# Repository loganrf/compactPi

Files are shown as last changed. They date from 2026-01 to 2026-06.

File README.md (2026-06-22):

# compactPi

compactPi is a project to develop a compact Raspberry Pi Compute Module carrier suitable for ArduPilot applications. It's primarily targeted at marine applications (ArduSub/ArduRover).

## Milestones

As of June 2026, these milestones are way out of date due to personal circumstances. As I get back up to speed there will be substantial updates to this timeline!

| # | Description | Estimated Time Frame| Status |
|---|---|---|---|
| 1 |Feature freeze | Mid-Feb | On Track |
| 2 |Schematic/layout draft ready for review | Early march | In Work |
| 3 |Gerbers ready for review | End of march | TBD |
| 4 |PCB Tape Out | Mid April | TBD |
| 5 |Board Fab & Build | June/July (assuming 30 day turn for initial prototypes to keep costs maneagable)| TBD |
| 6 |Validation/Verification Complete| TBD | TBD |
| 7 |V1.0 Design File Release| TBD (dependent on how well the first rev does) | TBD |

# Layout Study (PRELIMINARY)
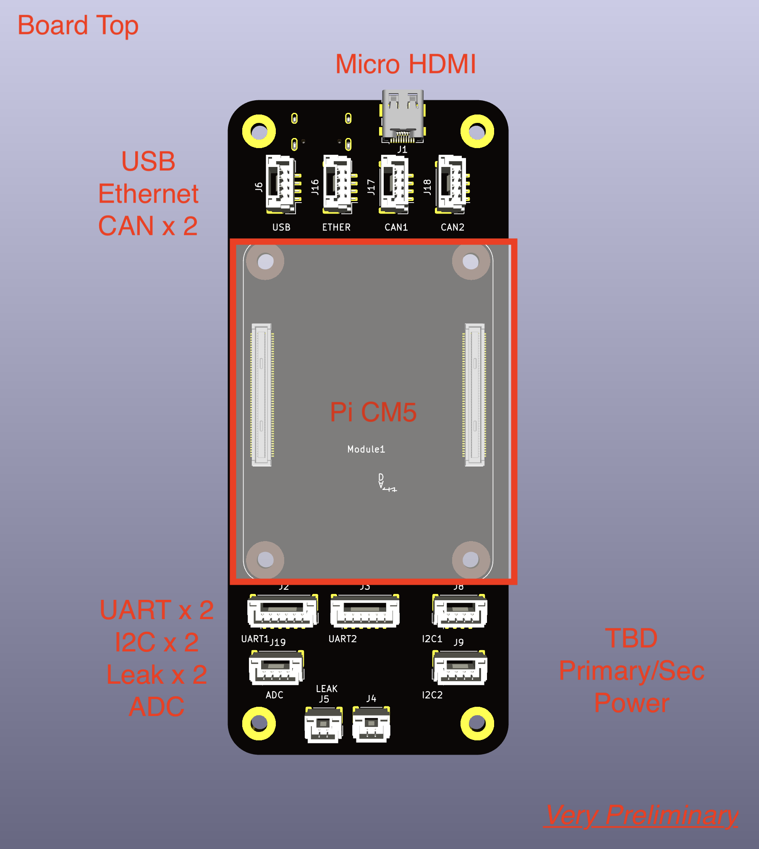
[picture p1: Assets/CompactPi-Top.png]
Top

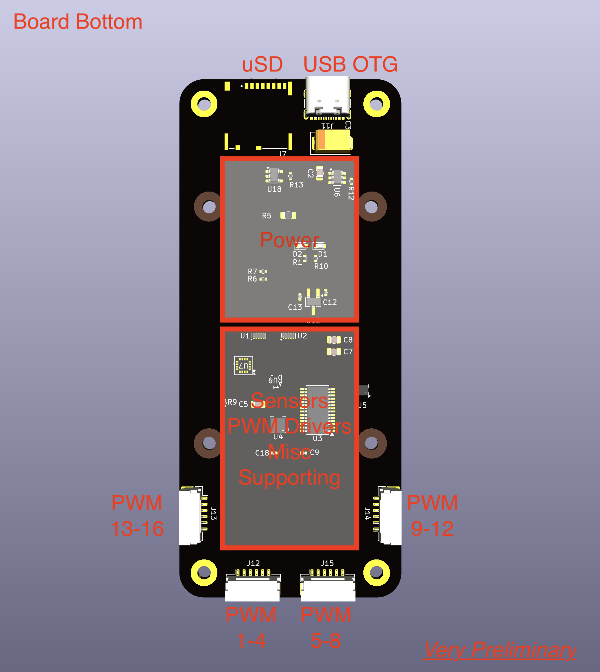
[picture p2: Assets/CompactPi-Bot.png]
Bottom


# Design Details (PROPOSED)

## Power/Physical
| # | Description | Value/Units | Notes |
|---|---|---|---|
| 1 |Input Voltage range| 6-25V | 2 independent inputs + USB-C PD option |
| 2 |Mainboard power dissipation | 25W | |
| 3 |Dimensions | 45mm x 105mm | Evaluating options for shrinking length without over-crowding connectors|

## Key Sensors
| # | Description | Part Number | 
|---|---|---|
| 1 |6 Axis IMU | ICM-20602 |
| 2 |3 Axis Magnetometer | MMC5983 |
| 3 |3 Axis Compass | AK09915 |
| 4 |Barometer | BMP280 |
| 5 |ADC | TBD |

## Interfaces
| # | Description | Form Factor | Qty | Notes |
|---|---|---|---|---|
| 1 |UART | JST-GH BM06B | 2 |  |
| 2 |I2C | JST-GH BM04B | 2 |  |
| 3 |SBUS | TBD |1| |
| 4 |5V PWM Quad Out | JST-GH BM06B | 4 | 4 PWM channels per connector, 16 total per carrier|
| 5 |Leak Sensor | JST-GH BM02B | 1 | |
| 6 |ADC | TBD | TBD| |
| 7 |HDMI | HDMI-C | 1 | |
| 8 |Ethernet 10/100| JST-GH BM04B | 1 | |
| 9 |USB| 1x JST-GH BM04B/ 1x USB-C OTG | 2 | |
| 10 |SD| micro-SD | 1 | |
| 11 |Power | TBD | 2 | |
| 12 |CAN Bus | JST-GH BM04B | 2 | |

# Stackup
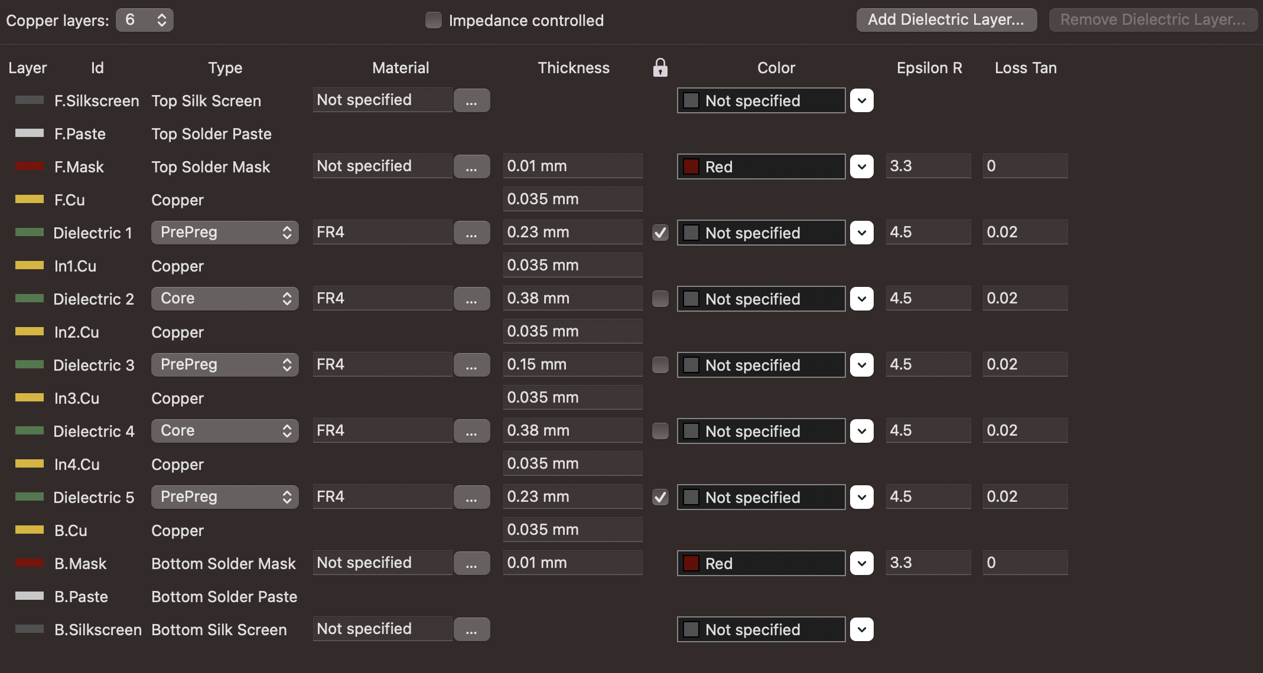
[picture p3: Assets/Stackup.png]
Stackup Diagram From KiCAD


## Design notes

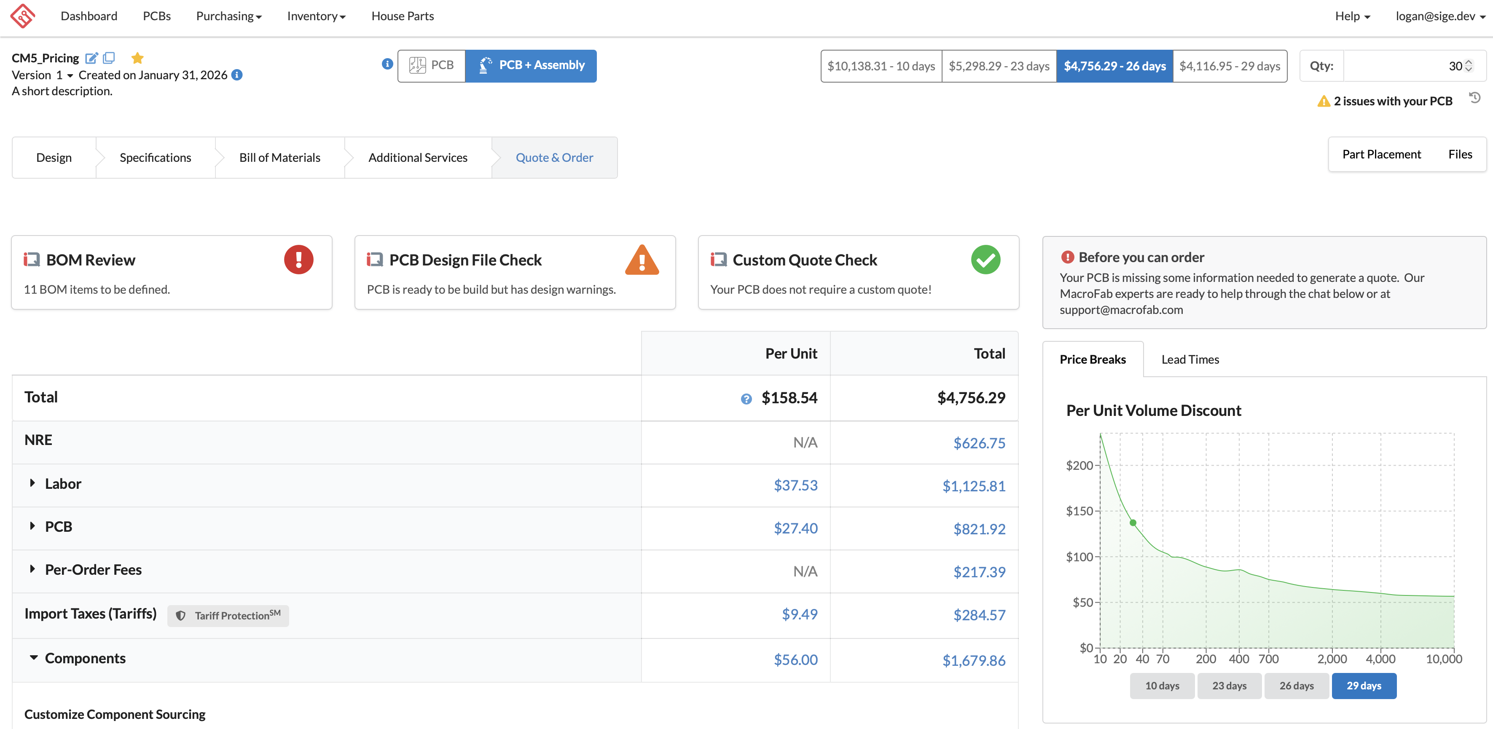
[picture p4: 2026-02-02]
Docs/Screenshot 2026-01-31 at 20.46.59.png

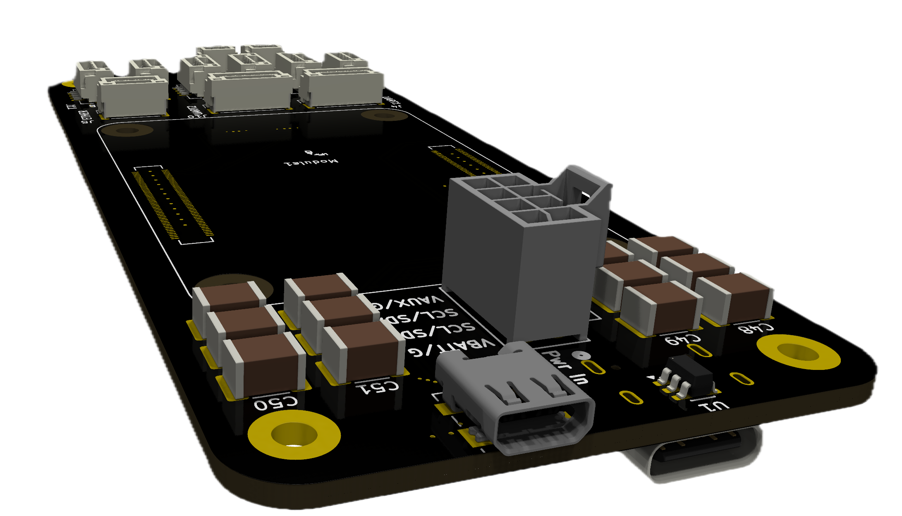
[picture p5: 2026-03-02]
Docs/compactPi-angle.png

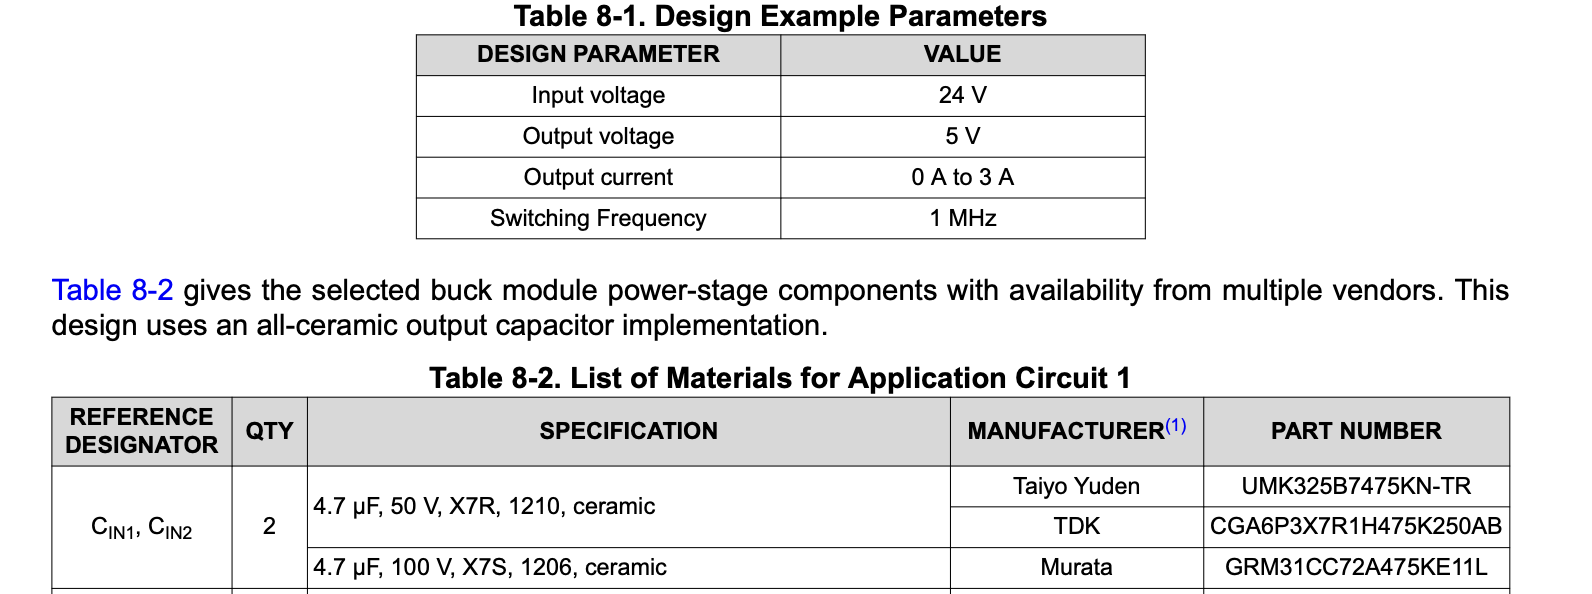
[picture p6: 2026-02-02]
Docs/Screenshot 2026-02-01 at 09.07.32.png

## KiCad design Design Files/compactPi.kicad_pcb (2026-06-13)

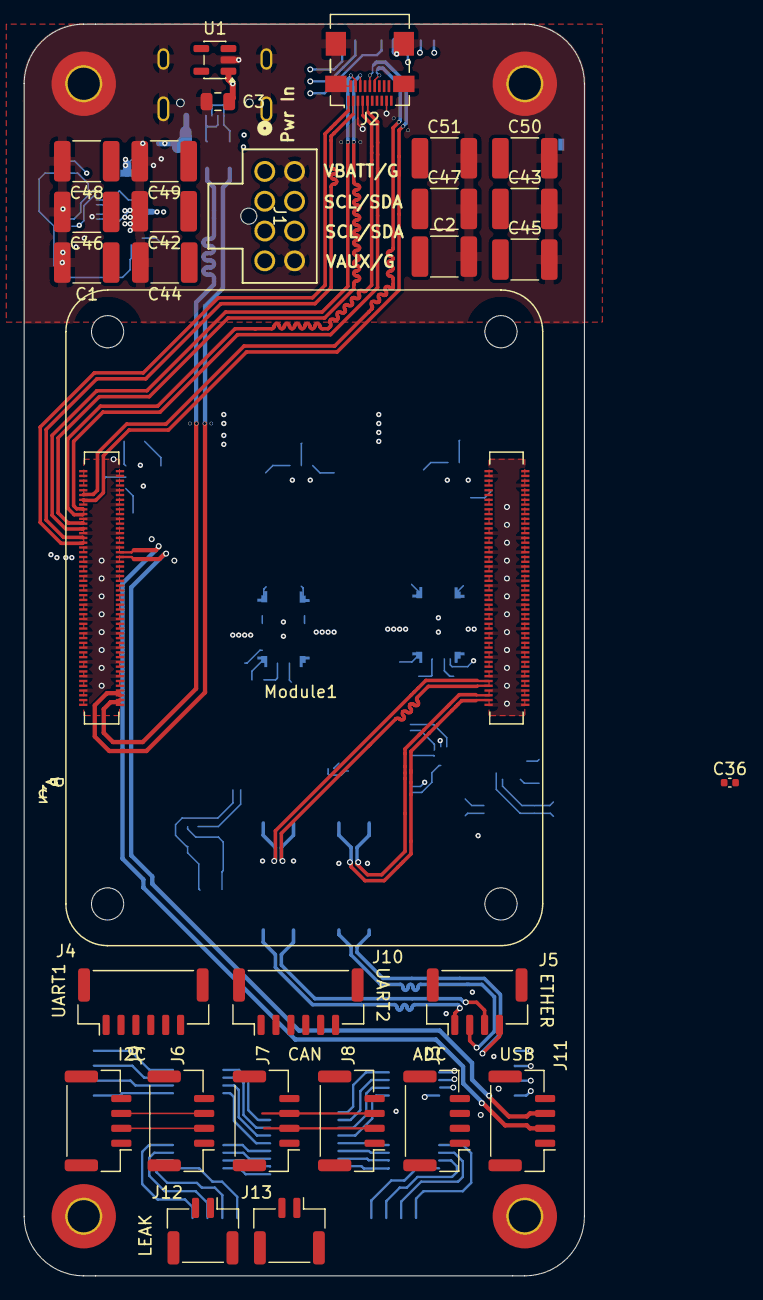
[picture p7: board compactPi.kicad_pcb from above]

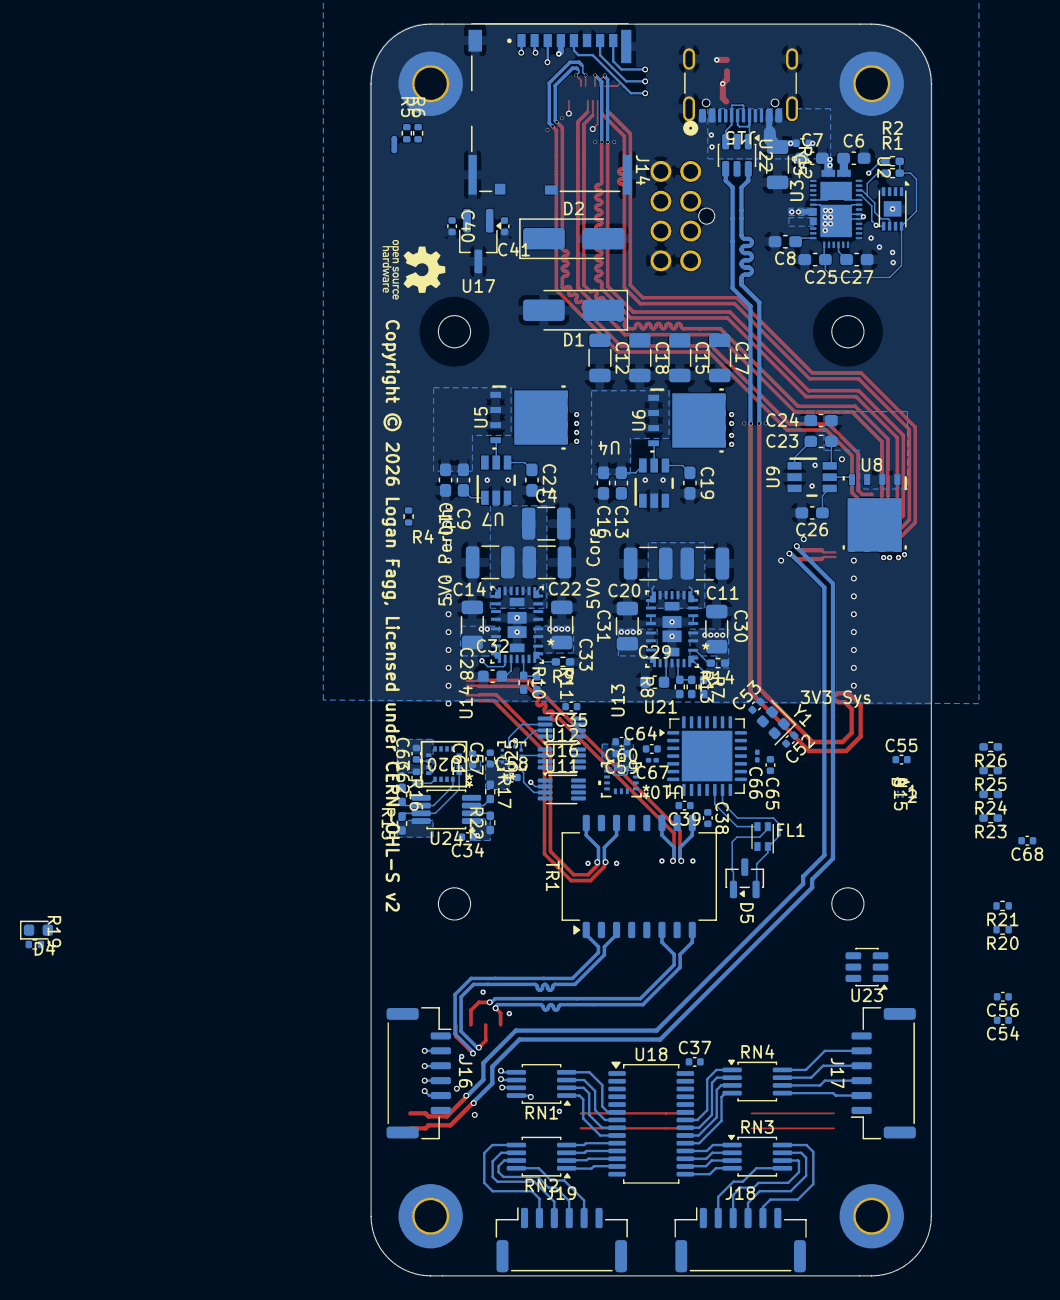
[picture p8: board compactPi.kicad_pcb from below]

Board: 6 copper layers, 47.0 x 105.0 mm, 152 parts (119 on the bottom side), 144 nets.

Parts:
C1, C2, C42, C43, C44, C45, C46, C47, C48, C49, C50, C51: 6.8uF; C_1812_4532Metric
C3: 10u; C_0805_2012Metric
C4, C11, C14, C20, C22: 47uF; C_1210_3225Metric
C5, C12, C15, C17, C18, C28, C30, C31, C33: 4.7uF; C_1206_3216Metric
C6, C7, C8, C9, C10, C13, C16, C19, C21, C23, C24, C25, C26, C27: 100nF; C_0603_1608Metric_Pad1.08x0.95mm_HandSolder
C29, C32: 1uF; C_0603_1608Metric
C34, C35, C36, C37, C38, C39, C54, C55, C57, C58, C59, C60, C61, C62, C64, C65: 100nF; C_0402_1005Metric
C40, C41: 100n; C_0402_1005Metric
C52, C53: 22pF; C_0402_1005Metric
C56: 1000pF; C_0402_1005Metric
C63: 10uF; C_0402_1005Metric
C66, C67: 10u; C_0201_0603Metric
C68: 47pF; C_0402_1005Metric
D1, D2: SMAJ26A; D_SMA_Handsoldering
D4: LED Red; LED_0603_1608Metric
D5: SZNUP2105L; SOT-23
FL1: Choke_CommonMode_FerriteCore_1234; L_CommonModeChoke_Coilcraft_0805USB
H1, H2, H3, H4: MountingHole_Pad; MountingHole_2.7mm_Pad_TopBottom
J1: 1053101208; CONN_SD-105310-100_08_MOL
J2: HDMI_A_1.4; HDMI_Micro-D_Molex_46765-0xxx
J3, J5, J6, J7, J8, J9, J11: Conn_01x04_MountingPin; JST_GH_BM04B-GHS-TBT_1x04-1MP_P1.25mm_Vertical
J4, J10: Conn_01x06_MountingPin; JST_GH_BM06B-GHS-TBT_1x06-1MP_P1.25mm_Vertical
J12, J13: Conn_01x02_MountingPin; JST_GH_BM02B-GHS-TBT_1x02-1MP_P1.25mm_Vertical
J14: Micro_SD_Card_Det; SDCARD_MOLEX_503398-1892
J15: USB_C_Receptacle_USB2.0; USB_C_Receptacle_GCT_USB4105-xx-A_16P_TopMnt_Horizontal
J16, J17, J18, J19: Conn_01x06_MountingPin; JST_GH_SM06B-GHS-TB_1x06-1MP_P1.25mm_Horizontal
Module1: ComputeModule5-CM5; Raspberry-Pi-5-Compute-Module
NT1: NetTie_2; NetTie-2_SMD_Pad0.5mm
R1, R2: R_US; R_0402_1005Metric_Pad0.72x0.64mm_HandSolder
R4: 10K 1%; R_0402_1005Metric
R5, R6, R12: 2.2K 1%; R_0402_1005Metric
R7, R9: 25.5k; R_0402_1005Metric_Pad0.72x0.64mm_HandSolder
R8, R11, R14, R15, R16, R17, R22, R23, R24, R26: 10k; R_0402_1005Metric_Pad0.72x0.64mm_HandSolder
R10, R13: 53.6k; R_0402_1005Metric_Pad0.72x0.64mm_HandSolder
R19: 1k; R_0402_1005Metric
R20, R21: 75; R_0402_1005Metric
R25: 120; R_0402_1005Metric_Pad0.72x0.64mm_HandSolder
RN1, RN2, RN3, RN4: R_Pack04; MSOP-8_3x3mm_P0.65mm
TR1: TG110-E050N5xx; Transformer_Ethernet_Halo_N5_SO-16_7.11x12.7mm
U1: RT9742GGJ5; SOT-23-5
U2: AT24CS64-MAHM; DFN-8-1EP_3x2mm_P0.5mm_EP1.3x1.5mm
U3: TPS25751D
U4, U7, U9: LM74700QDBVRQ1; DBV0006A_M
U5, U6, U8: CSD18511Q5A; DQJ0008A
U10: BMI270; BMI270_BOS
U11, U12, U16: 74LVC2T45DC; VSSOP-8_2.3x2mm_P0.5mm
U13, U14: TLVM13630RDHR; B0QFN30_RDH_TEX
U15: AK09918C; BGA4_WL-CSP_AKM
U17: RT9742SNGV; TSOT-23_HandSoldering
U18: PCA9685PW; TSSOP-28_4.4x9.7mm_P0.65mm
U20: MMC5983MA; MMC5983MA_MEM
U21: MCP25625x-x-ML; QFN-28-1EP_6x6mm_P0.65mm_EP4.25x4.25mm
U22, U23: WE-TVS-82400102; SOT-23-6
U24: TCA9517ADGK; VSSOP-8_3x3mm_P0.65mm
U25: BMP390; 10LGA_2X2X0p75_BOS
Y1: Crystal_GND24_Small; Crystal_SMD_2016-4Pin_2.0x1.6mm

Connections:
/1V8: C34.1, C55.1, C57.1, C58.1, C59.1, C60.1, Module1.88 (+1.8v_(Output)), Module1.90 (+1.8v_(Output)), R17.1, R22.1, U10.5 (VDDIO), U10.8 (VDD), U11.1 (VCCA), U12.1 (VCCA), U15.B1 (VDD), U16.8 (VCCB), U24.1 (VCCA), U25.1 (VDDIO), U25.10 (VDD)
/3V3: C35.1, C36.1, C37.1, C38.1, C39.1, C61.1, D4.2 (A), Module1.84 (+3.3v_(Output)), Module1.86 (+3.3v_(Output)), NT1.1, R4.1, R15.1, R16.1, R26.2, U1.5 (IN), U11.8 (VCCB), U12.8 (VCCB), U16.1 (VCCA), U18.28 (VDD), U20.2 (VDD), U21.11 (V_{IO}), U24.8 (VCCB)
/5V0_CORE: Module1.77 (+5v_(Input)), Module1.79 (+5v_(Input)), Module1.81 (+5v_(Input)), Module1.83 (+5v_(Input)), Module1.85 (+5v_(Input)), Module1.87 (+5v_(Input))
/5V0_PERIPHERAL: C41.1, C64.1, C65.1, C66.1, C67.1, J4.1, J6.1, J7.1, J8.1, J9.1, J10.1, J11.1, J16.1, J17.1, J18.1, J19.1, U17.1 (IN), U21.3 (V_{DD}), U21.19 (V_{DDA})
/Autopilot Interfaces/CANH_PC: FL1.1, U21.13 (CANH)
/Autopilot Interfaces/CAN_CLKO: C68.1, U21.6 (CLKOUT)
/Autopilot Interfaces/CAN_H: D5.1 (K), FL1.2, J7.2, J8.2, R25.1
/Autopilot Interfaces/CAN_L: D5.2 (K), FL1.4, J7.3, J8.3, R25.2
/Autopilot Interfaces/CAN_L_PC: FL1.3, U21.12 (CANL)
/Autopilot Interfaces/CAN_PULL_HI: R26.1, U21.7 (~Tx0RTS), U21.8 (~Tx1RTS), U21.9 (~Tx2RTS), U21.23 (~Rx1BF), U21.24 (~Rx0BF)
/Autopilot Interfaces/CAN_RST: R23.1, U21.2 (~RESET)
/Autopilot Interfaces/CAN_RX: U21.5 (RxCAN), U21.10 (R_{XD})
/Autopilot Interfaces/CAN_STBY: R24.1, U21.15 (STBY)
/Autopilot Interfaces/CAN_TX: U21.4 (TxCAN), U21.16 (T_{XD})
/Autopilot Interfaces/OSC_1: C53.1, U21.21 (OSC1), Y1.3
/Autopilot Interfaces/OSC_2: C52.1, U21.20 (OSC2), Y1.1
/Autopilot Sensors/CS_PRES_1V8: U11.2 (1A), U25.6 (CSB)
/Autopilot Sensors/I2C_SCL_1V8: R22.2, U10.13 (SCX), U15.A2 (SCL), U24.2 (SCLA)
/Autopilot Sensors/I2C_SDA_1V8: R17.2, U10.14 (SDX), U15.B2 (SDA), U24.3 (SDAA)
/Autopilot Sensors/INT_PRES_1V8: U16.6 (2B), U25.7 (INT)
/Autopilot Sensors/MAG_VDDIO: C62.1, U20.13 (VDDIO)
/Autopilot Sensors/SPI_CIPO_1V8: U16.7 (1B), U25.5 (SDO)
/Autopilot Sensors/SPI_COPI_1V8: U12.2 (1A), U25.4 (SDI)
/Autopilot Sensors/SPI_SCK_1V8: U11.3 (2A), U25.2 (SCK)
/CM5 GPIO Ethernet SDIO/GPIO_VREF: Module1.78 (GPIO_VREF(1.8v/3.3v_Input)), NT1.2, R5.1, R6.1
/CM5 GPIO Ethernet SDIO/ID_SC: Module1.35 (ID_SC), R6.2
/CM5 GPIO Ethernet SDIO/ID_SD: Module1.36 (ID_SD), R5.2
/CM5 GPIO Ethernet SDIO/SD_CLK: J14.5 (CLK), Module1.57 (SD_CLK)
/CM5 GPIO Ethernet SDIO/SD_CMD: J14.3 (CMD), Module1.62 (SD_CMD)
/CM5 GPIO Ethernet SDIO/SD_DAT0: J14.7 (DAT0), Module1.63 (SD_DAT0)
/CM5 GPIO Ethernet SDIO/SD_DAT1: J14.8 (DAT1), Module1.67 (SD_DAT1)
/CM5 GPIO Ethernet SDIO/SD_DAT2: J14.1 (DAT2), Module1.69 (SD_DAT2)
/CM5 GPIO Ethernet SDIO/SD_DAT3: J14.2 (DAT3/CD), Module1.61 (SD_DAT3)
/CM5 GPIO Ethernet SDIO/SD_PWR: C3.1, J14.4 (VDD), U1.1 (OUT)
/CM5 GPIO Ethernet SDIO/SD_PWR_ON: Module1.75 (SD_PWR_ON), R4.2, U1.4 (EN)
/CM5 GPIO Ethernet SDIO/TRD0_N: Module1.10 (Ethernet_Pair0_N), TR1.11 (RD-)
/CM5 GPIO Ethernet SDIO/TRD0_P: Module1.12 (Ethernet_Pair0_P), TR1.9 (RD+)
/CM5 GPIO Ethernet SDIO/TRD0_TX_N: J5.3, TR1.6 (RX-)
/CM5 GPIO Ethernet SDIO/TRD0_TX_P: J5.1, TR1.8 (RX+)
/CM5 GPIO Ethernet SDIO/TRD1_N: Module1.6 (Ethernet_Pair1_N), TR1.16 (TD-)
/CM5 GPIO Ethernet SDIO/TRD1_P: Module1.4 (Ethernet_Pair1_P), TR1.14 (TD+)
/CM5 GPIO Ethernet SDIO/TRD1_RX_N: J5.4, TR1.1 (TX-)
/CM5 GPIO Ethernet SDIO/TRD1_RX_P: J5.2, TR1.3 (TX+)
/CM5 GPIO Ethernet SDIO/nPWR_LED: Module1.95 (LED_nPWR), R19.2
/CM5 USB HDMI/HDMI0_CEC: J2.13 (CEC), Module1.151 (HDMI0_CEC)
/CM5 USB HDMI/HDMI0_CK_N: J2.12 (CK-), Module1.190 (HDMI0_CLK_N)
/CM5 USB HDMI/HDMI0_CK_P: J2.10 (CK+), Module1.188 (HDMI0_CLK_P)
/CM5 USB HDMI/HDMI0_D0_N: J2.9 (D0-), Module1.184 (HDMI0_TX0_N)
/CM5 USB HDMI/HDMI0_D0_P: J2.7 (D0+), Module1.182 (HDMI0_TX0_P)
/CM5 USB HDMI/HDMI0_D1_N: J2.6 (D1-), Module1.178 (HDMI0_TX1_N)
/CM5 USB HDMI/HDMI0_D1_P: J2.4 (D1+), Module1.176 (HDMI0_TX1_P)
/CM5 USB HDMI/HDMI0_D2_N: J2.3 (D2-), Module1.172 (HDMI0_TX2_N)
/CM5 USB HDMI/HDMI0_D2_P: J2.1 (D2+), Module1.170 (HDMI0_TX2_P)
/CM5 USB HDMI/HDMI0_HOTPLUG: J2.19 (HPD/HEAC-), Module1.153 (HDMI0_HOTPLUG)
/CM5 USB HDMI/HDMI0_SCL: J2.15 (SCL), Module1.200 (HDMI0_SCL)
/CM5 USB HDMI/HDMI0_SDA: J2.16 (SDA), Module1.199 (HDMI0_SDA)
/CM5 USB HDMI/HDMI_5v: C40.1, J2.18 (+5V), U17.2 (OUT)
/CM5 USB HDMI/USB3-1-D_N: J11.2, Module1.165 (USB3-1-D_N)
/CM5 USB HDMI/USB3-1-D_P: J11.3, Module1.163 (USB3-1-D_P)
/I2C_EXT_SCL1: J6.2, J9.2, Module1.56 (GPIO3)
/I2C_EXT_SDA1: J6.3, J9.3, Module1.58 (GPIO2)
/I2C_INT_SCL0: Module1.80 (SCL0), R15.2, U20.1 (SCL/SPI_SCK), U24.7 (SCLB)
/I2C_INT_SDA0: Module1.82 (SDA0), R16.2, U20.16 (SDA/SPI_SDI), U24.6 (SDAB)
/I2C_PWM_SCL: Module1.37 (GPIO7), U18.26 (SCL)
/I2C_PWM_SDA: Module1.30 (GPIO6), U18.27 (SDA)
/PWM IO/PWM_01_PR: RN1.3 (R3.1), U18.7 (LED1)
/PWM IO/PWM_02_PR: RN1.2 (R2.1), U18.8 (LED2)
/PWM IO/PWM_03_PR: RN1.1 (R1.1), U18.9 (LED3)
/PWM IO/PWM_04_PR: RN2.4 (R4.1), U18.10 (LED4)
/PWM IO/PWM_05_PR: RN2.3 (R3.1), U18.11 (LED5)
/PWM IO/PWM_06_PR: RN2.2 (R2.1), U18.12 (LED6)
/PWM IO/PWM_07_PR: RN2.1 (R1.1), U18.13 (LED7)
/PWM IO/PWM_08_PR: RN3.4 (R4.1), U18.15 (LED8)
/PWM IO/PWM_09_PR: RN3.3 (R3.1), U18.16 (LED9)
/PWM IO/PWM_10_PR: RN3.2 (R2.1), U18.17 (LED10)
/PWM IO/PWM_11_PR: RN3.1 (R1.1), U18.18 (LED11)
/PWM IO/PWM_12_PR: RN4.4 (R4.1), U18.19 (LED12)
/PWM IO/PWM_13_PR: RN4.3 (R3.1), U18.20 (LED13)
/PWM IO/PWM_14_PR: RN4.2 (R2.1), U18.21 (LED14)
/PWM IO/PWM_15_PR: RN4.1 (R1.1), U18.22 (LED15)
/PWM IO/PWM_PR_00: RN1.4 (R4.1), U18.6 (LED0)
/Power/5V0_C_FB: R8.1, R13.2, U13.25 (FB)
/Power/5V0_C_RAW: C11.1, C20.1, R13.1, U13.7 (VOUT), U13.8 (VOUT), U13.9 (VOUT), U13.10 (VOUT), U13.12 (VOUT), U13.13 (VOUT), U13.14 (VOUT), U13.15 (VOUT), U13.22 (VLDOIN), U13.30 (VOUT)
/Power/5V0_C_RT: R7.1, U13.1 (RT)
/Power/5V0_C_VCC: C29.1, U13.23 (VCC)
/Power/5V0_EN: R14.2, U13.2 (EN/SYNC)
/Power/5V0_P_FB: R10.2, R11.1, U14.25 (FB)
/Power/5V0_P_RAW: C4.1, C14.1, C22.1, R10.1, U14.7 (VOUT), U14.8 (VOUT), U14.9 (VOUT), U14.10 (VOUT), U14.12 (VOUT), U14.13 (VOUT), U14.14 (VOUT), U14.15 (VOUT), U14.22 (VLDOIN), U14.30 (VOUT)
/Power/5V0_P_RT: R9.1, U14.1 (RT)
/Power/5V0_P_VCC: C32.1, U14.23 (VCC)
/Power/5V_PERIPHERAL: U3.34 (PP5V), U3.35 (PP5V)
/Power/I2Cc_SCL: R1.2, U2.6 (SCL), U3.17 (I2Cc_SCL)
/Power/I2Cc_SDA: R2.2, U2.5 (SDA), U3.16 (I2Cc_SDA)
/Power/LDO_1V5: C27.1, U3.4 (LDO_1V5)
/Power/USB_DRAIN: U3.15 (DRAIN), U3.30 (DRAIN), U3.40 (DRAIN_PAD)
/Power/USB_LDO_3V3: C25.1, R1.1, R2.1, U2.8 (VCC), U3.1 (LDO_3V3)
/Power/VIN_3V3: C8.1, U3.38 (VIN_3V3)
/Power/V_AUX: C2.1, C12.1, C13.1, C16.1, C18.1, C43.1, C45.1, C47.1, C50.1, C51.1, D1.1 (A1), J1.4, U4.3 (EN), U4.6 (ANODE), U6.1 (S), U6.2 (S), U6.3 (S)
/Power/V_BATT: C1.1, C9.1, C10.1, C15.1, C17.1, C42.1, C44.1, C46.1, C48.1, C49.1, D2.1 (A1), J1.1, U5.1 (S), U5.2 (S), U5.3 (S), U7.3 (EN), U7.6 (ANODE)
/Power/V_COMMON: C19.1, C21.1, C26.1, C28.1, C30.1, C31.1, C33.1, R14.1, U4.4 (CATHODE), U5.5 (D), U5.6 (D), U5.7 (D), U5.8 (D), U5.9 (D), U6.5 (D), U6.6 (D), U6.7 (D), U6.8 (D), U6.9 (D), U7.4 (CATHODE), U8.5 (D), U8.6 (D), U8.7 (D), U8.8 (D), U8.9 (D), U9.4 (CATHODE), U13.3 (VIN), U13.4 (VIN), U13.18 (VIN), U13.19 (VIN), U14.3 (VIN), U14.4 (VIN), U14.18 (VIN), U14.19 (VIN)
/Power/V_USB: C6.1, C23.1, C24.1, U3.20 (PPHV), U3.21 (PPHV), U3.22 (PPHV), U8.1 (S), U8.2 (S), U8.3 (S), U9.3 (EN), U9.6 (ANODE)
/SPI_CAN_CE0: Module1.49 (GPIO18), U21.1 (~CS)
/SPI_CAN_CIPO: Module1.27 (GPIO20), U21.28 (SO)
/SPI_CAN_COPI: Module1.26 (GPIO19), U21.27 (SI)
/SPI_CAN_SCK: Module1.25 (GPIO21), U21.26 (SCK)
/SPI_INT_CE0: Module1.39 (GPIO8), U11.7 (1B)
/SPI_INT_CIPO: Module1.44 (GPIO10), U16.2 (1A)
/SPI_INT_COPI: Module1.40 (GPIO9), U12.7 (1B)
/SPI_INT_SCK: Module1.38 (GPIO11), U11.6 (2B)
/USB2_N: J15.A7 (D-), J15.B7 (D-), U22.1
/USB2_P: J15.A6 (D+), J15.B6 (D+), U22.3
/USB2a_N: Module1.103 (USB2_N), U22.6
/USB2a_P: Module1.105 (USB2_P), U22.4
/VBUS: C5.1, C7.1, J15.A4 (VBUS), J15.A9 (VBUS), J15.B4 (VBUS), J15.B9 (VBUS), R12.1, U3.23 (VBUS_IN), U3.24 (VBUS_IN), U3.25 (VBUS_IN), U3.32 (VBUS), U3.33 (VBUS)
/VBUS_EN: Module1.111 (VBUS_EN), U14.2 (EN/SYNC)
GND: C1.2, C2.2, C3.2, C4.2, C5.2, C6.2, C7.2, C8.2, C10.2, C11.2, C12.2, C14.2, C15.2, C16.2, C17.2, C18.2, C19.2, C20.2, C21.2, C22.2, C24.2, C25.2, C26.2, C27.2, C28.2, C29.2, C30.2, C31.2, C32.2, C33.2, C34.2, C35.2, C36.2, C37.2, C38.2, C39.2, C40.2, C41.2, C42.2, C43.2, C44.2, C45.2, C46.2, C47.2, C48.2, C49.2, C50.2, C51.2, C52.2, C53.2, C54.2, C55.2, C56.2, C57.2, C58.2, C59.2, C60.2, C61.2, C62.2, C63.2, C64.2, C65.2, C66.2, C67.2, C68.2, D1.2 (A2), D2.2 (A2), D5.3 (A), H1.1 (1_1), H2.1 (1_1), H3.1 (1_1), H4.1 (1_1), J1.5, J1.8, J2.2 (D2S), J2.5 (D1S), J2.8 (D0S), J2.11 (CKS), J2.17 (GND), J2.SH, J4.6, J6.4, J7.4, J8.4, J9.4, J10.6, J11.4, J14.6 (VSS), J14.11 (SHIELD), J15.A1 (GND), J15.A12 (GND), J15.B1 (GND), J15.B12 (GND), J15.S1 (SHIELD), J16.6, J17.6, J18.6, J19.6, Module1.1 (GND), Module1.2 (GND), Module1.7 (GND), Module1.8 (GND), Module1.13 (GND), Module1.14 (GND), Module1.22 (GND), Module1.23 (GND), Module1.32 (GND), Module1.33 (GND), Module1.42 (GND), Module1.43 (GND), Module1.52 (GND), Module1.53 (GND), Module1.59 (GND), Module1.60 (GND), Module1.65 (GND), Module1.66 (GND), Module1.71 (GND), Module1.74 (GND), Module1.93 (nRPIBOOT), Module1.98 (GND), Module1.107 (GND), Module1.108 (GND), Module1.113 (GND), Module1.114 (GND), Module1.119 (GND), Module1.120 (GND), Module1.125 (GND), Module1.126 (GND), Module1.131 (GND), Module1.132 (GND), Module1.137 (GND), Module1.138 (GND), Module1.144 (GND), Module1.150 (GND), Module1.155 (GND), Module1.156 (GND), Module1.161 (GND), Module1.162 (GND), Module1.167 (GND), Module1.168 (GND), Module1.173 (GND), Module1.174 (GND), Module1.179 (GND), Module1.180 (GND), Module1.185 (GND), Module1.186 (GND), Module1.191 (GND), Module1.192 (GND), Module1.197 (GND), Module1.198 (GND), R7.2, R8.2, R9.2, R11.2, R12.2, R23.2, R24.2, U1.2 (GND), U2.4 (GND), U2.9 (GND), U3.11 (GND), U3.12 (GND), U3.14 (GND), U3.31 (GND), U3.39 (GND), U4.2 (GND), U7.2 (GND), U9.2 (GND), U10.6 (GNDIO), U10.7 (GND), U11.4 (GND), U11.5 (DIR), U12.4 (GND), U12.5 (DIR), U12.6 (2B), U13.5 (PGND), U13.6 (PGND), U13.16 (PGND), U13.17 (PGND), U13.24 (AGND), U13.26 (PG), U13.27 (AGND), U13.28 (PGND), U13.29 (PGND), U14.5 (PGND), U14.6 (PGND), U14.16 (PGND), U14.17 (PGND), U14.24 (AGND), U14.26 (PG), U14.27 (AGND), U14.28 (PGND), U14.29 (PGND), U15.A1 (VSS), U16.4 (GND), U16.5 (DIR), U17.3 (GND), U18.14 (VSS), U20.9 (GND), U20.11 (GND), U21.18 (V_{SS}), U21.22 (GND), U21.29 (EP), U24.4 (GND), U25.3 (VSS), U25.8 (VSS), U25.9 (VSS), Y1.2 (G), Y1.4 (G)
unnamed: C56.1, R20.1, R21.1
unnamed: D4.1 (K), R19.1
unnamed: J16.2, RN1.5 (R4.2)
unnamed: J16.3, RN1.6 (R3.2)
unnamed: J16.4, RN1.7 (R2.2)
unnamed: J16.5, RN1.8 (R1.2)
unnamed: J17.2, RN4.5 (R4.2)
unnamed: J17.3, RN4.6 (R3.2)
unnamed: J17.4, RN4.7 (R2.2)
unnamed: J17.5, RN4.8 (R1.2)
unnamed: J18.2, RN3.5 (R4.2)
unnamed: J18.3, RN3.6 (R3.2)
unnamed: J18.4, RN3.7 (R2.2)
unnamed: J18.5, RN3.8 (R1.2)
unnamed: J19.2, RN2.5 (R4.2)
unnamed: J19.3, RN2.6 (R3.2)
unnamed: J19.4, RN2.7 (R2.2)
unnamed: J19.5, RN2.8 (R1.2)
unnamed: C54.1, TR1.10 (C_RD), TR1.15 (C_TD)
unnamed: R20.2, TR1.7 (C_RX)
unnamed: R21.2, TR1.2 (C_TX)
unnamed: U4.5 (GATE), U6.4 (G)
unnamed: C13.2, U4.1 (VCAP)
unnamed: U5.4 (G), U7.5 (GATE)
unnamed: C9.2, U7.1 (VCAP)
unnamed: U8.4 (G), U9.5 (GATE)
unnamed: C23.2, U9.1 (VCAP)
unnamed: C63.1, U20.10 (CAP)

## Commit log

2026-01-25 Revise design details and specifications in README
    Updated design details and specifications for the compactPi project, including power, physical dimensions, key sensors, and interfaces.
2026-01-25 Add CAN Bus entry to the README table
2026-01-26 Add milestones section to README
    Added milestones section with estimated time frames and statuses for project development.
2026-02-02 Updated input voltage range to reflect dropout voltage of the power architecture (6V instead of 5V)
2026-02-08 Initial design file commit
    [CM5_GPIO.kicad_sch, CM5_HighSpeed.kicad_sch, Power.kicad_sch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]
2026-02-08 file reorg
    [CM5_GPIO.kicad_sch, CM5_HighSpeed.kicad_sch, Power.kicad_sch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]
2026-02-09 Added additional ground vias to ethernet nets
    [compactPi.kicad_pcb]
2026-02-10 Added stackup
    [compactPi.kicad_pcb]
2026-02-10 updated skews
    [compactPi.kicad_pcb]
2026-03-02 Prelim work on autopilot sensors complete
    [CM5_GPIO.kicad_sch, compactPi.kicad_sch, sensors.kicad_sch]
2026-03-02 Fixed reversed I2C tranlator
    [sensors.kicad_sch]
2026-03-12 Continued adding GPIO interfaces
    [CM5_GPIO.kicad_sch, compactPi.kicad_sch]
2026-03-15 More interface interconnects
    [CM5_GPIO.kicad_sch, CM5_HighSpeed.kicad_sch, Power.kicad_sch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]
2026-03-15 Fixed power & GPIO nets
    Added PWM I2C Bus
    Replaced global power labels on the sensor page with hierarchical pins & page labels
    Cleaned up CM5 GPIO block sheet
    [CM5_GPIO.kicad_sch, CM5_HighSpeed.kicad_sch, ap_io.kicad_sch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]
2026-03-31 Additional layout updates
    [CM5_GPIO.kicad_sch, CM5_HighSpeed.kicad_sch, Power.kicad_sch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]
2026-03-31 Provisional CAN interface design/layout. Probably need to move more north
    [autopilot_conn.kicad_sch, compactPi.kicad_pcb]
2026-06-13 SD pwr routed
    [CM5_GPIO.kicad_sch, compactPi.kicad_pcb, compactPi.kicad_sch]

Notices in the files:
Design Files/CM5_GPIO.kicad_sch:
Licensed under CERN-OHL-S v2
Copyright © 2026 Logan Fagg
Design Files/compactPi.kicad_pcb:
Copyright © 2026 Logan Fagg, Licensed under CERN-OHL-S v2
